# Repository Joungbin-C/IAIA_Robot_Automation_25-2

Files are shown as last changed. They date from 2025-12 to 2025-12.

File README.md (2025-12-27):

# 25-2 Robot Automation: Battery Winding Manipulation Automation

**Date:** 2025/12/27

**Author:** Joungbin Choi, Hyeongyu Seo, Inyeop Kim

**Advisor:** Professor YK Kim

**Github:** [repository link](https://github.com/Joungbin-C/IAIA_Robot_Automation_25-2)

***

[**Demo Video**](https://youtu.be/vMVNzXjdA7o)

[**Report Link**](https://github.com/Joungbin-C/IAIA_Robot_Automation_25-2/tree/main/Report)

[**Source Code Link**](https://github.com/Joungbin-C/IAIA_Robot_Automation_25-2/tree/main/src)

[**Summary PPT Link**](https://github.com/Joungbin-C/IAIA_Robot_Automation_25-2/tree/main/Docs(PPT))

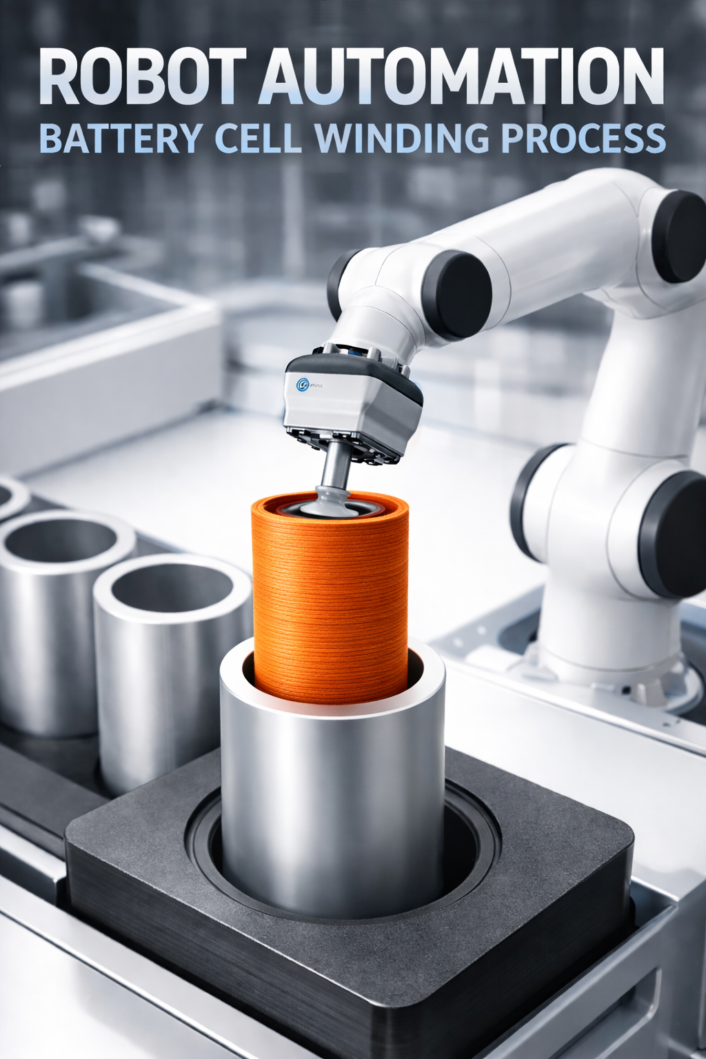
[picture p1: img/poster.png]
poster


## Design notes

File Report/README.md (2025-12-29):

# 25-2 Robot Automation: Battery Winding Manipulation Automation

**Date:** 2025/12/27

**Author:** Joungbin Choi, Hyeongyu Seo, Inyeop Kim

**Advisor:** Professor YK Kim

**Github:** [repository link](https://github.com/Joungbin-C/IAIA_Robot_Automation_25-2)

**Demo Video:** [**Demo Video**](https://youtu.be/vMVNzXjdA7o)

***

## I. Introduction

With the rapid growth of the electric vehicle (EV) market, the secondary battery industry has emerged as a key strategic sector. It is projected that by 2030, electric vehicles will account for more than 40% of the global automotive market, leading to a significant increase in battery production demand[1]. However, conventional battery cell assembly and disassembly processes remain highly dependent on manual labor, resulting in limitations in productivity, process consistency, and quality control. In particular, as the importance of battery recycling and safe disassembly increases, there is a growing demand for intelligent automation systems capable of handling precise and complex operations beyond simple assembly tasks.

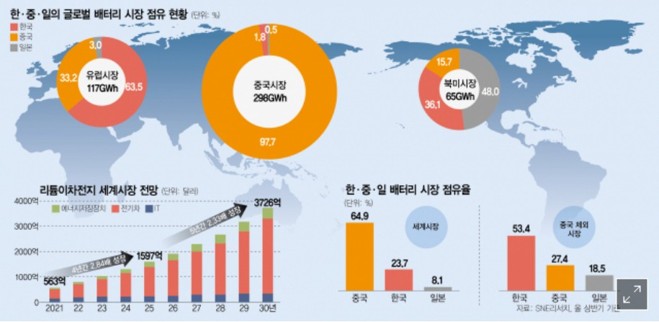
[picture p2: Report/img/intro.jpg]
intro


This project aims to address these challenges by developing an **automated battery cell winding process using industrial robots integrated with machine vision and artificial intelligence technologies**. By combining robotic manipulation, sensor-based detection nodes, state diagram–based control logic, and camera-based recognition of battery cells and winding components, the project seeks to transform a labor-intensive process into a high-speed, high-precision automated system. Through this approach, the feasibility of improving productivity, reliability, and safety in battery manufacturing and recycling processes is investigated.

## II. Problem Statement

### 1. Project Objectives

The main objectives of this project are as follows:

1. **Implementation of Automated Assembly and Disassembly of Battery Cell Winding Processes**
   To automate the assembly and disassembly of battery cells and winding components using industrial robots, thereby minimizing human error and improving repeatability.
2. **Development of a Machine Vision–Based Recognition System**
   To detect battery cell positions, orientations, and conditions (normal or defective) using camera-based vision systems and AI models, and to integrate the recognition results into the robot control system.
3. **Design of Robot Control Logic and State Diagrams**
   To design structured state diagrams that manage process flow and ensure stable coordination between sensor detection nodes and robotic actions.
4. **Verification of Process Reliability and Performance**
   To experimentally evaluate the success rate, accuracy, and operational stability of the automated system and assess its applicability to real industrial environments.

### 2. Expected Outcomes

The expected outcomes of this project are as follows:

1. **Improved Productivity and Operational Efficiency**
   By replacing manual labor with robotic automation, continuous operation beyond traditional working hours becomes possible, significantly increasing overall productivity.
2. **Enhanced Accuracy and Quality Consistency**
   The automated system is expected to achieve a high success rate in assembly and disassembly tasks, while the machine vision system enables reliable identification of normal and abnormal battery cells, excluding specific inclusion cases.
3. **Reduced Labor Dependency and Improved Workplace Safety**
   Automating repetitive and potentially hazardous battery handling processes reduces worker exposure to risk and lowers dependence on skilled manual labor.
4. **Scalability for Battery Recycling and Future Smart Factory Applications**
   The proposed system can be extended to battery disassembly and recycling processes, providing a technological foundation for advanced smart factory and sustainable battery production systems.

### 3. Evaluation Index

| Process | Target |
| --- | --- |
| **UR5 Robot Operation** | - Bracket detection success rate ≥ 98% <br />- Cell box detection success rate = 100% <br />- Pick and Place success rate ≥ 95% <br />- Stopper linkage success rate = 100% <br />- Assembly/Disassembly process completion time ≤ 1 minute |
| **Indy10 Robot Operation** | - Cell orientation detection success rate = 100% <br />- Foreign object detection success rate ≥ 95% <br />- Defective cell detection success rate ≥ 95% <br />- Stopper linkage success rate = 100% <br />- Winding assembly/disassembly process completion time ≤ 1 minute |
| **Defect Detection** | - Defect detection success rate (cylindrical surface) ≥ 95% <br />- Defect detection success rate (flat surface) ≥ 80% |

### 4. Hardware

materials

These are materials for manipulation. A bracket is moving with slide rail and cells will be putted on it. Lastly, winds will be assembled or disassembled with cells. 

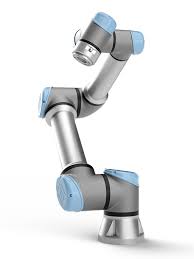
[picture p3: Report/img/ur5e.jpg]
ur5e


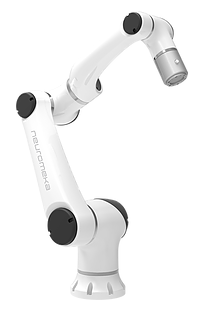
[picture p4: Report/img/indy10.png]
indy10


UR5e(upper image) and Indy10(bottom image) are utilized for assembling and disassembling manipulation. Overall, UR5e is used to pick-and-place cells on the bracket or get off cells from bracket. Indy10 is used to assemble or disassemble winds from cells. If there is a defected cell, Indy10 get rid of it from the bracket. 

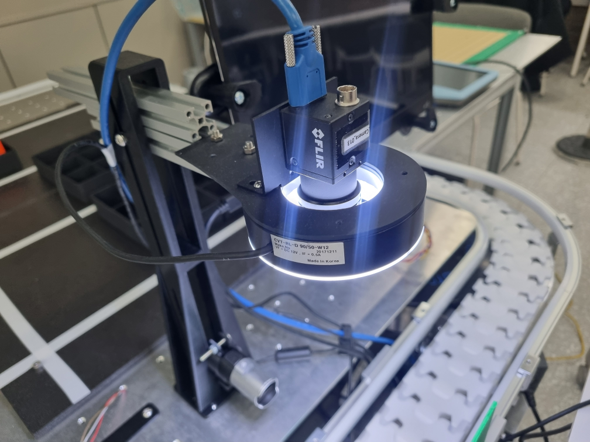
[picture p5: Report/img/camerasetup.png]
camerasetup


This is setup for machine vision to check the state of cells. There are two machine vision cameras: top-view and side-view. Top view camera checks for a circularity of cells and side camera checks for defects on the side of cells.

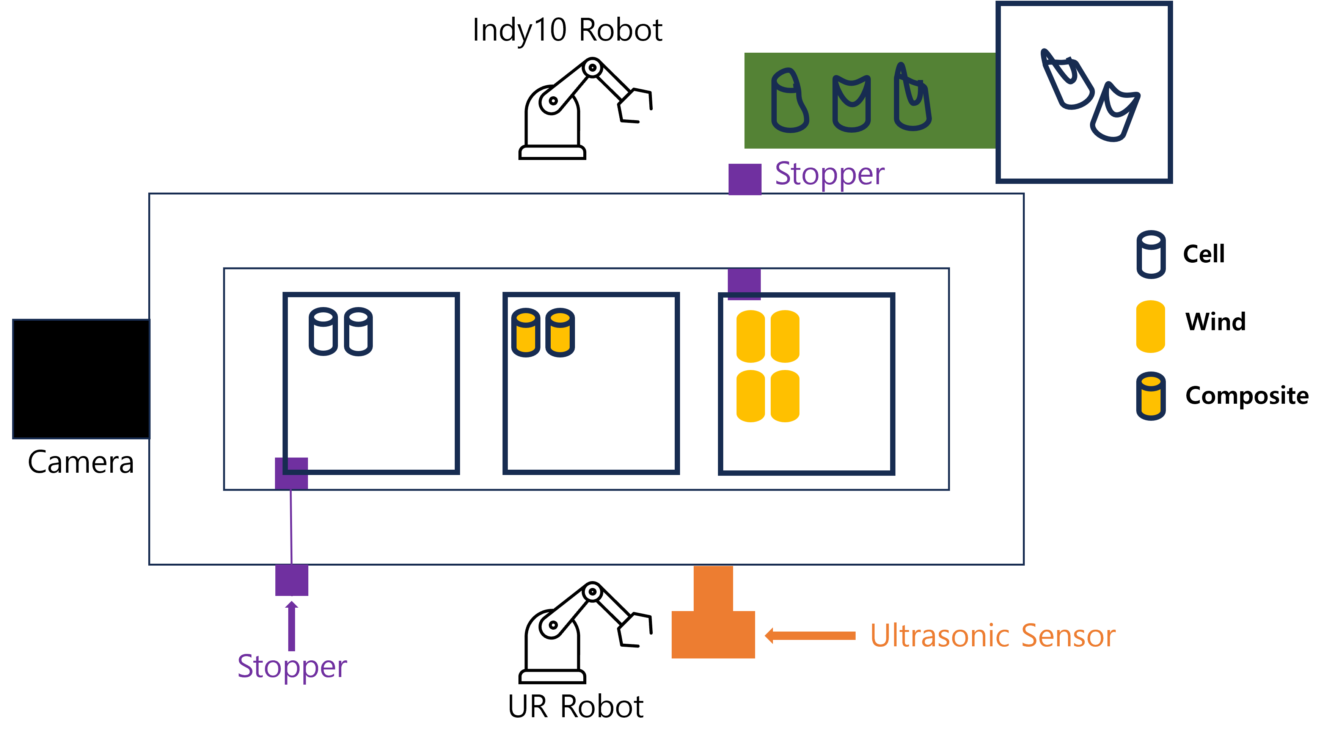
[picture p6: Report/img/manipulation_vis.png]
manipulation_vis


This is overall setup for battery wind manipulation. 

## III. Individual Report
**[UR5e](https://github.com/Joungbin-C/IAIA_Robot_Automation_25-2/tree/main/Report/Report_(Dis)assembly_Automation_Process/Report_(Dis)Assembly_Automation.md)**

**[Indy10](https://github.com/Joungbin-C/IAIA_Robot_Automation_25-2/blob/main/Report/Report_(De)Compose_process/Report_(De)Compose_process.md)**

**[Machine Vision](https://github.com/Joungbin-C/IAIA_Robot_Automation_25-2/blob/main/Report/Report_MachineVision_Process/Report_MachineVision_Process.md)**

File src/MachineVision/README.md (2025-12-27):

# Windows에서 PySpin 가상환경 설치 가이드

## 0. 사전 준비

1. **카메라 드라이버 & Spinnaker SDK 설치**
   - PySpin 버전과 **동일한 버전의 Spinnaker SDK**를 먼저 설치
   - 예: PySpin 3.0.0.0 → **Spinnaker SDK 3.0.0.0**
   - [PySpin 및 SDK 다운로드 링크](https://www.teledynevisionsolutions.com/ko-kr/support/support-center/software-firmware-downloads/iis/download-the-latest-spinnaker-software-development-kit/spinnaker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)
2. **Python 버전 확인**
   - 지원 버전: **3.5 ~ 3.8, 3.10**
   - 권장: **Python 3.10 (64-bit)** (우분투 20.04이면 3.8 (64-bit) 추천)
   - Python 설치 시 반드시 **64-bit**로 설치
   - 환경 변수에 파이썬이 등록 되어있어야함

------

## 1. Python 설치 확인

```
python --version
```

또는 Python 3.10 명시:

```
py -3.10 --version

# Ubuntu Version
py -3.8 --version
```

------

## 2. 콘다 설치

이 가이드에선 콘다가 미리 설치 되었다는 가정으로 진행

------

## 3. 가상환경 생성 (conda)

Python 3.10 기준 예시:

```
conda create -n pyspin python=3.10 -y

# Ubuntu Version
conda create -n pyspin python=3.8 -y
```

------

## 4. 가상환경 활성화

```
conda activate pyspin
```

성공하면 프롬프트 앞에 `(pyspin)` 표시됨:

```
(pyspin) C:\pyspin_project>
```

------

## 5. pip 최신화

```
python -m ensurepip
python -m pip install --upgrade pip
```

------

## 6. PySpin Wheel 설치

### PySpin wheel 파일 준비

Wheel 파일 위치로 이동

```
cd C:\path\to\spinnaker_python_wheel
```

whl파일 확인

예시:

```
spinnaker_python-3.0.0.0-cp310-cp310-win_amd64.whl
```

반드시 확인:

- `cp310` → Python 3.10
- `win_amd64` → 64-bit Windows

Unbuntu 20.04이면:
- `cp38` → Python 3.8
- 'linux_x86_64` → 64-bit Linux

### 설치

```
pip install spinnaker_python-3.x.x.x-cp310-cp310-win_amd64.whl
```

(실제 파일명으로 변경)

------

## 7. 설치 확인

```
python -c "import PySpin; print(PySpin.__version__)"
```

에러 없으면 성공

------

## 8. 예제 실행

Spinnaker SDK 또는 PySpin 압축 안의 예제 사용:

```
python Examples\Python3\Acquisition.py
```

또는 직접 테스트:

```
import PySpin

system = PySpin.System.GetInstance()
cam_list = system.GetCameras()
print("Number of cameras:", cam_list.GetSize())

cam_list.Clear()
system.ReleaseInstance()
```

------

## 9. 프로젝트를 위한 환경 설치

```
pip install numpy==2.2.6
pip install opencv-python-headless==4.10.0.84
pip install ultralytics==8.3.232
pip install PyQt5==5.15.11
pip install Pillow==9.2.0
```

## 10. 코드 실행 방법

깃허브에 `src/MachineVsion/AcquireAndDisplay_Final.py`을 spinnaker_python 파일에서 `Examples/Python3`에 옮긴 후 실행

## 11. 환경 비활성화

```
deactivate
```

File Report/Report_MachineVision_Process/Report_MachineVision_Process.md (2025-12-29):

# 25-2 Robot Automation - Machine Vision(Cell Defect Detecting)

**Date:** 2025/12/25

**Author:** Joungbin Choi

**Github:** [repository link](https://github.com/Joungbin-C/IAIA_Robot_Automation_25-2/tree/main)

**Demo Video:** [Youtube link](https://youtu.be/vMVNzXjdA7o)

***

## I. Introduction

With the rapid growth of the electric vehicle (EV) market, the secondary battery industry has emerged as a key strategic sector. It is projected that by 2030, electric vehicles will account for more than 40% of the global automotive market, leading to a significant increase in battery production demand[1]. However, conventional battery cell assembly and disassembly processes remain highly dependent on manual labor, resulting in limitations in productivity, process consistency, and quality control. In particular, as the importance of battery recycling and safe disassembly increases, there is a growing demand for intelligent automation systems capable of handling precise and complex operations beyond simple assembly tasks.

This project aims to address these challenges by developing an **automated battery cell winding process using industrial robots integrated with machine vision and artificial intelligence technologies**. By combining robotic manipulation, sensor-based detection nodes, state diagram–based control logic, and camera-based recognition of battery cells and winding components, the project seeks to transform a labor-intensive process into a high-speed, high-precision automated system. Through this approach, the feasibility of improving productivity, reliability, and safety in battery manufacturing and recycling processes is investigated.

## II. Problem Statement

### 1. Project Objectives

The main objectives of this project are as follows:

1. **Implementation of Automated Assembly and Disassembly of Battery Cell Winding Processes**
    To automate the assembly and disassembly of battery cells and winding components using industrial robots, thereby minimizing human error and improving repeatability.
2. **Development of a Machine Vision–Based Recognition System**
    To detect battery cell positions, orientations, and conditions (normal or defective) using camera-based vision systems and AI models, and to integrate the recognition results into the robot control system.
3. **Design of Robot Control Logic and State Diagrams**
    To design structured state diagrams that manage process flow and ensure stable coordination between sensor detection nodes and robotic actions.
4. **Verification of Process Reliability and Performance**
    To experimentally evaluate the success rate, accuracy, and operational stability of the automated system and assess its applicability to real industrial environments.

### 2. Expected Outcomes

The expected outcomes of this project are as follows:

1. **Improved Productivity and Operational Efficiency**
    By replacing manual labor with robotic automation, continuous operation beyond traditional working hours becomes possible, significantly increasing overall productivity.
2. **Enhanced Accuracy and Quality Consistency**
    The automated system is expected to achieve a high success rate in assembly and disassembly tasks, while the machine vision system enables reliable identification of normal and abnormal battery cells, excluding specific inclusion cases.
3. **Reduced Labor Dependency and Improved Workplace Safety**
    Automating repetitive and potentially hazardous battery handling processes reduces worker exposure to risk and lowers dependence on skilled manual labor.
4. **Scalability for Battery Recycling and Future Smart Factory Applications**
    The proposed system can be extended to battery disassembly and recycling processes, providing a technological foundation for advanced smart factory and sustainable battery production systems.

### 3. Evaluation Index

| Process | Target |
| --- | --- |
| **UR5 Robot Operation** | - Bracket detection success rate ≥ 98% <br />- Cell box detection success rate = 100% <br />- Pick and Place success rate ≥ 95% <br />- Stopper linkage success rate = 100% <br />- Assembly/Disassembly process completion time ≤ 1 minute |
| **Indy10 Robot Operation** | - Cell orientation detection success rate = 100% <br />- Foreign object detection success rate ≥ 95% <br />- Defective cell detection success rate ≥ 95% <br />- Stopper linkage success rate = 100% <br />- Winding assembly/disassembly process completion time ≤ 1 minute |
| **Defect Detection** | - Defect detection success rate (cylindrical surface) ≥ 95% <br />- Defect detection success rate (flat surface) ≥ 80% |

## III. Requirements

Write a list of HW/SW requirements.

### 1. Hardware List

* Computer
* 2 Spinnaker Cameras
* Slide Rail
* 2 Stepper Motors
* 2 Ardunio Boards
* 2 Ultrasonic Sensors
* Windings, Cells, Brakets
* Light

### 2. Software List

* CUDA 13.0
* cudatoolkit 12.6
* Python 3.10.8
* Pytorch 2.7.0+cu128
* YOLO v8
* Spinnaker SDK
* Spinnaker Python
* Numpy 2.2.6
* opencv python headless 4.10.0.84
* ultralytics 8.3.232
* PyQT5 5.15.11
* Pillow 9.2.0

### 3. Dataset

For surface detection of the cell, the dataset is customized. There are 4 classes: rugged, pitted, inclusion, and scratch

**Dataset link:** [download link](https://universe.roboflow.com/jb-edsws/surface-detecting-bdnua/dataset/2) 

***

## IV. Installation and Procedure

### 1. Hardware Setup

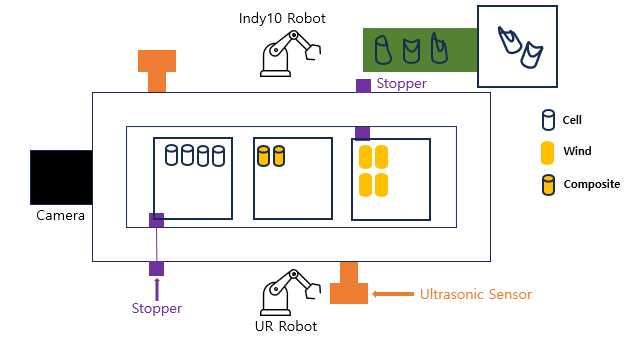
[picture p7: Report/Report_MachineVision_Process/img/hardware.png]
hardware


**Figure 1. Hardware Overview**

This image show hardware Setup:

1. UR5 and Indy10 robots are placed between the stopper(stepper motors) and ultrasonic sensors. If ultrasonic sensors detect the bracket, stopper is closed.
2. Cameras are placed upper and side of the rail. Upper camera check the circularity of the cell and side camera check the surface of the cell.

camerasetup

**Figure 2. Camera Setup**

### 2. Software Installation

For software installation of machine vision part, you can find the instruction in this [github link](https://github.com/Joungbin-C/IAIA/tree/main/Project/Project2_RobotAutomation)

### 3. Data Preparation

This dataset is customized and total number of data is 1,701.

train data : 90%

validation data : 7% 

test data : 3%

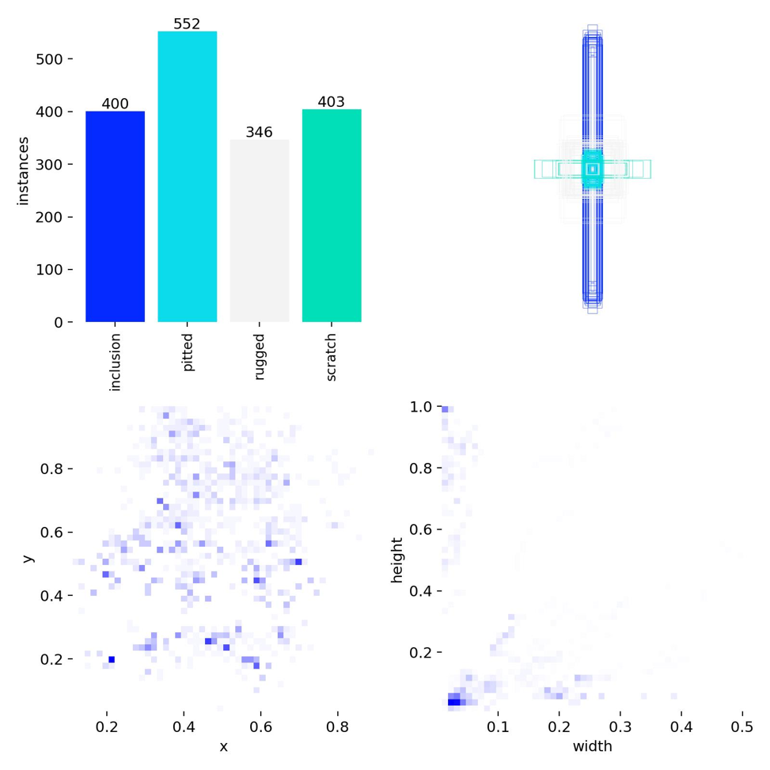
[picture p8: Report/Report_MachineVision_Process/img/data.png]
data


**Figure 3. Dataset Distribution**

The original data was unbalanced. Inclusion and scratch are much less than others, so oversampling was proceeded. Final balanced dataset is shown in **Figure 3**.

### 4. Train model

YOLO (You Only Look Once) is a real-time object detection model that simultaneously performs object localization and classification in a single forward pass of a neural network. By processing the entire image at once rather than using a multi-stage detection pipeline, YOLO achieves high inference speed with relatively low computational complexity. The model divides the input image into a grid and predicts bounding boxes, confidence scores, and class probabilities for each grid cell, enabling efficient and accurate object detection. Due to its fast response time and robustness, YOLO is widely used in applications such as industrial automation, robotic pick-and-place systems, defect detection, and real-time machine vision–based control systems[2].

**Table 1. Hyperparameter of Surface Defect Detection Model**

| Parameter | Number |
| --- | --- |
| Model | YOLOv8s |
| Epoch | 100 |
| Batch | 8 |
| Optimizer | AdamW(lr=0.001) |
| Early Stop  | 20 |
| Final Epoch | 53 |

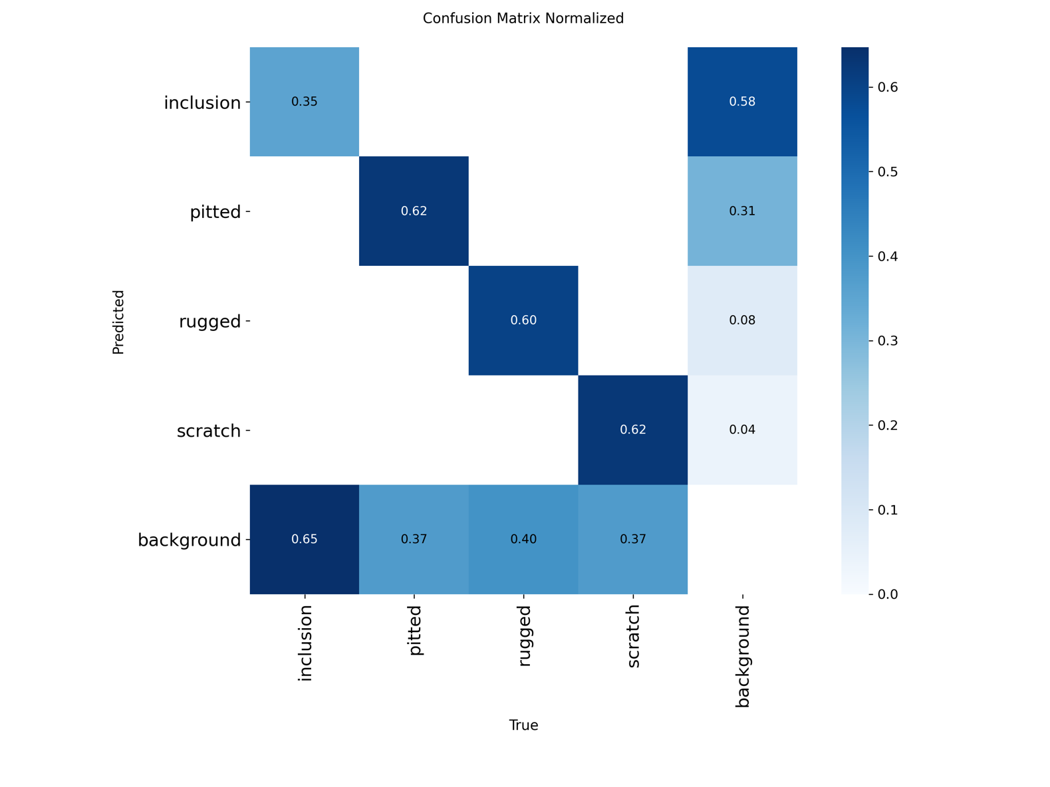
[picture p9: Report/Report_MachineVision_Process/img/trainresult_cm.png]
trainresult_cm


**Figure 4. Training Result Confusion Matrix**

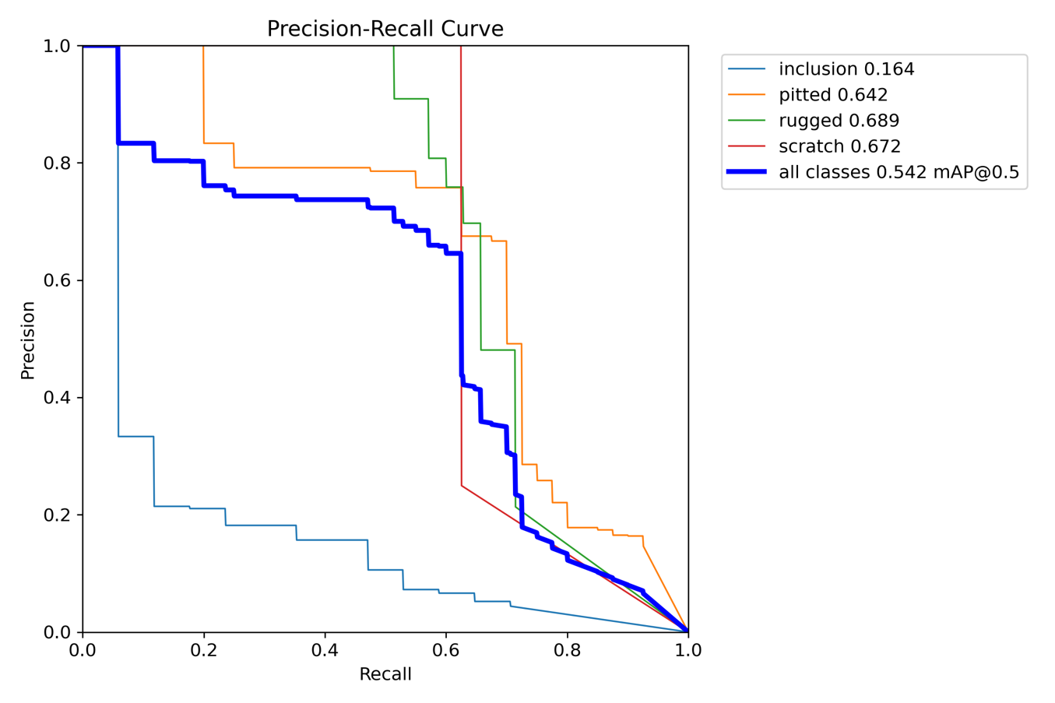
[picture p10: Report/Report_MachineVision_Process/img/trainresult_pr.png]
trainresult_pr


**Figure 5. PR Curve Graph**

**Table 2. Defect Classes**

| Class | Description |
| --- | --- |
| Rugged | Rough surfeace |
| Pitted | Indented defect |
| Inclusion | Foreign inclusion |
| Scratch | Scratch defect |

Thin and elongated inclusion defects are difficult to detect because their small size, low contrast, and extreme aspect ratios are poorly represented in bounding box–based object detection models, leading to feature loss and insufficient learning during training[5].

***

## V. Method

### 1. Overview

This study proposes an automated battery cell inspection system that integrates a **dual-camera machine vision setup with traditional image processing techniques and a deep learning–based surface defect detection model**. The system consists of two industrial FLIR cameras, OpenCV-based geometric analysis, a YOLO-based deep learning model, and a socket-based communication interface for external device control.

Camera 1 is responsible for **cell geometry analysis**, including circular shape detection, edge-based crack inspection, and thickness measurement. Camera 2 performs **surface defect detection** using a YOLO-based object detection model. The inspection process follows a state-based logic in which two consecutive cells (Cell 1 and Cell 2) are evaluated and their results are combined to generate a final decision flag.

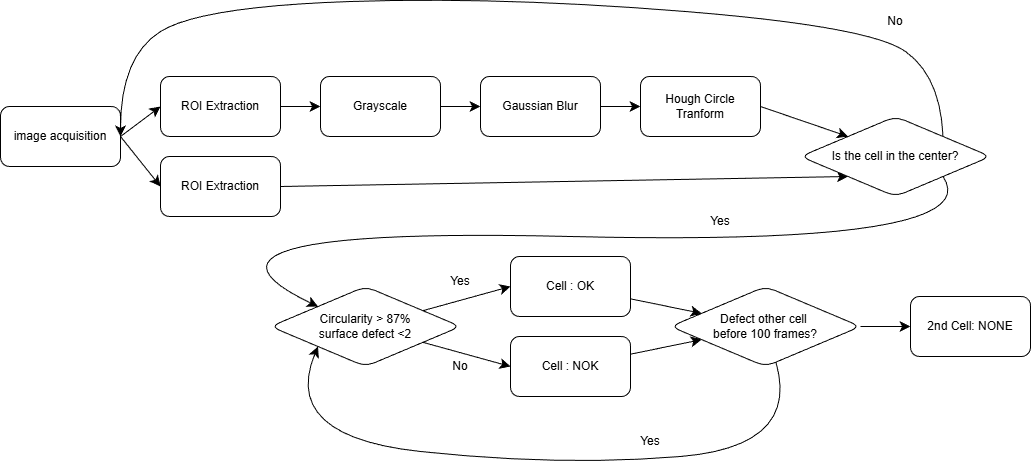
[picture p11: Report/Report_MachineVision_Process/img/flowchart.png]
flowchart


**Figure 6. Flow Chart**

### 2. Preprocessing

Preprocessing steps were designed separately for each camera according to its inspection purpose.

For Camera 1, a fixed-size **region of interest (ROI)** centered in the image was extracted to remove unnecessary background information. The ROI image was converted to grayscale and smoothed using Gaussian blur to reduce noise. Circular features of the battery cell were detected using the **Hough Circle Transform**, and the detected outer circle was used to define an edge ring region. **Canny edge detection** was applied within this region to emphasize crack-related features[3]. 

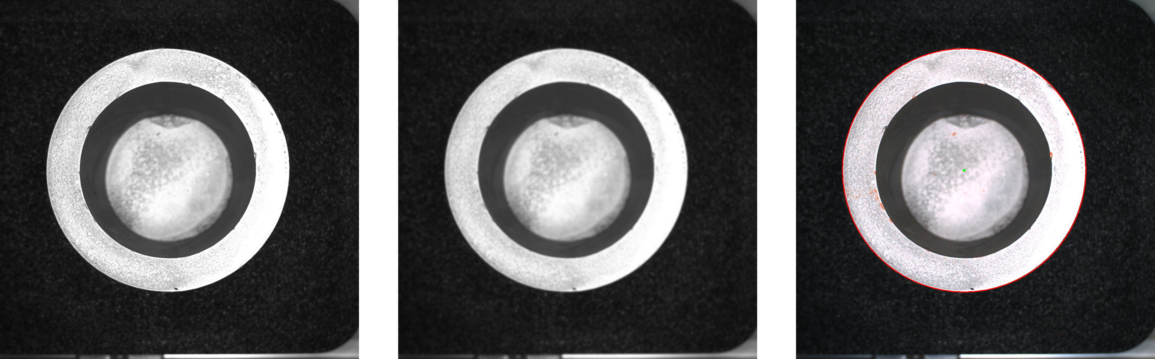
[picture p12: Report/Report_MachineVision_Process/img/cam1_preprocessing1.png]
cam1_preprocessing1


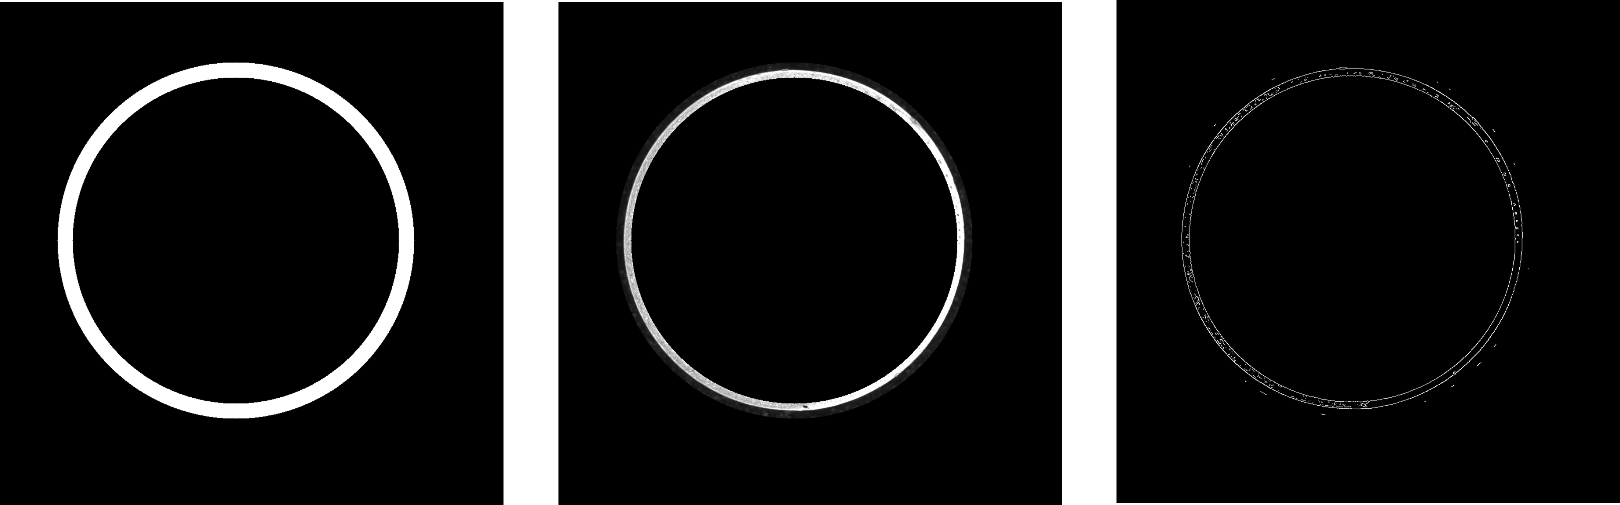
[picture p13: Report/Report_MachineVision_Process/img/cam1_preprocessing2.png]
cam1_preprocessing2


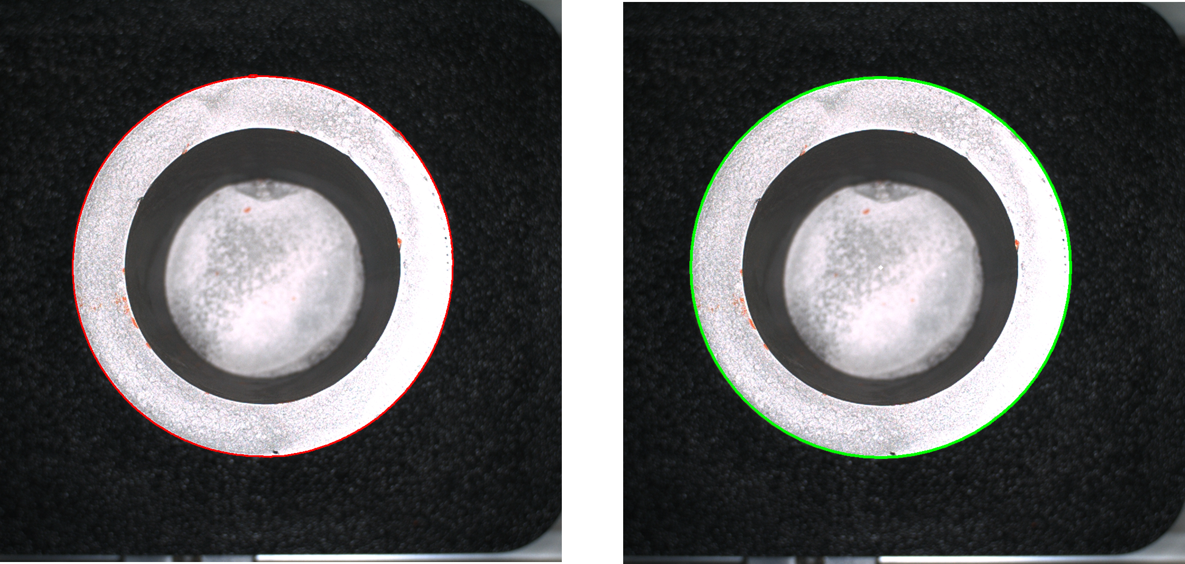
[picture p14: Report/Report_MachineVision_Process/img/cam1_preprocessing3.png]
cam1_preprocessing3


**Figure 7. Preprocessing: Grayscale, Gaussian blur, Hough Circle,  Ring Mask, Ring ROI, Canny Edge,  Contour, and Result**

Contour extraction and circularity analysis were then used to determine the presence of edge cracks.
$$
Circularity= \frac{4πA} {P^2}
$$
For Camera 2, a centered ROI was extracted from the original color image and directly passed to the YOLO model without additional color conversion. This approach preserves surface texture and intensity variations, which are critical for surface defect detection. Input resizing and normalization were handled internally by the YOLO framework.

### 3. Deep Learning Model

A **YOLOv8-based object detection model** was employed for surface defect detection[4]. YOLO (You Only Look Once) is a single-stage object detection framework that simultaneously predicts object locations and class probabilities in a single forward pass, enabling real-time performance.

cam2_result (2)

**Figure 8. Surface Detection Result**

YOLOv8 offers improved detection accuracy and computational efficiency compared to previous YOLO versions, making it suitable for real-time industrial inspection systems. In this study, a fine-tuned YOLOv8 model trained on a battery surface defect dataset was used. The model outputs bounding boxes and confidence scores for detected surface defects, and the number of detected defects is used as a criterion for surface quality assessment.

### 4. Postprocessing

#### **Algorithm #1: Cell Geometry and Edge-Based Defect Decision**

The first postprocessing algorithm evaluates the geometric validity of the detected battery cell and determines edge-related defects. The detected outer circle must satisfy predefined radius and area thresholds to be considered valid. An edge ring region is then analyzed using contour-based circularity metrics to identify potential cracks. Final decisions are made only when the detected cell is sufficiently centered in the image, reducing false detections caused by partial or misaligned cells.

#### **Algorithm #2: Cell Pairing and Decision Fusion Algorithm**

The second algorithm fuses the inspection results of two consecutive cells (Cell 1 and Cell 2). Each cell is classified as OK or NOK, and their combined results are mapped to predefined numeric flags for external communication. A timeout mechanism is implemented to handle cases where the second cell is not detected within a specified number of frames, ensuring robust operation in continuous production environments.

### 5. Experiment Method

Experiments were conducted under continuous image acquisition conditions that simulate real industrial inspection environments. Two FLIR cameras were operated in continuous acquisition mode, and multiple samples of normal and defective battery cells were tested.

The evaluation metrics included:

- Circle detection success rate
- Surface defect detection success rate using YOLO

## VI. Results and Analysis

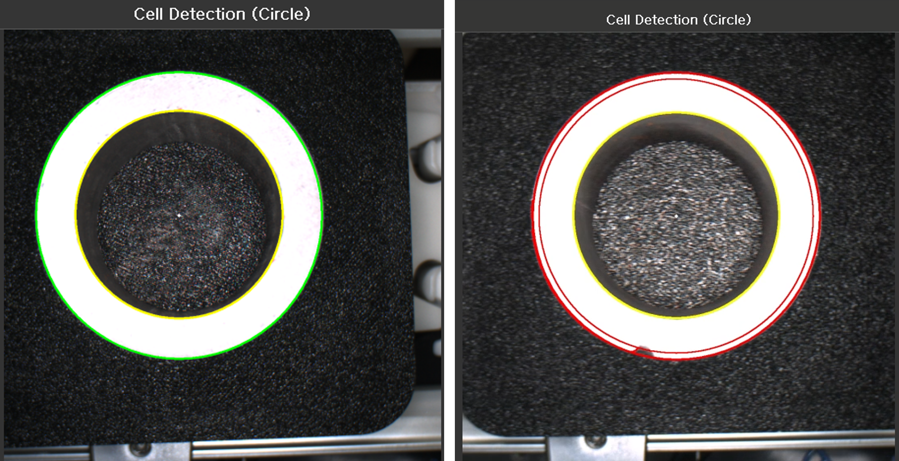
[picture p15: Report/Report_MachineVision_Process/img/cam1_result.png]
cam1_result


**Figure 9. Top Camera Result**

The accuracy of the circularity-based decision logic was evaluated through a total of 105 inspection trials. Among these, 53 defective cells and 52 normal cells were passed through the system to verify the correctness of the classification results. The experimental results showed that both normal cells (Cell Okay) and defective cells (Cell Not Okay) achieved accuracy levels exceeding the target threshold of 95%. This indicates that the circularity-based decision method provides high reliability and robustness for detecting edge cracks on battery cells. In particular, the method maintained consistent performance even under conditions with image noise and variations in illumination.

**Table 3. Circularity Accuracy Table**

| Classification | Target Accuracy [%] | Detection Result | Result Accuracy [%] |
| --- | --- | --- | --- |
| Cell Okay | ≥ 95 | 102 / 105 | **97.14** |
| Cell Not Okay  | ≥ 95 | 100 / 105 | **95.24** |

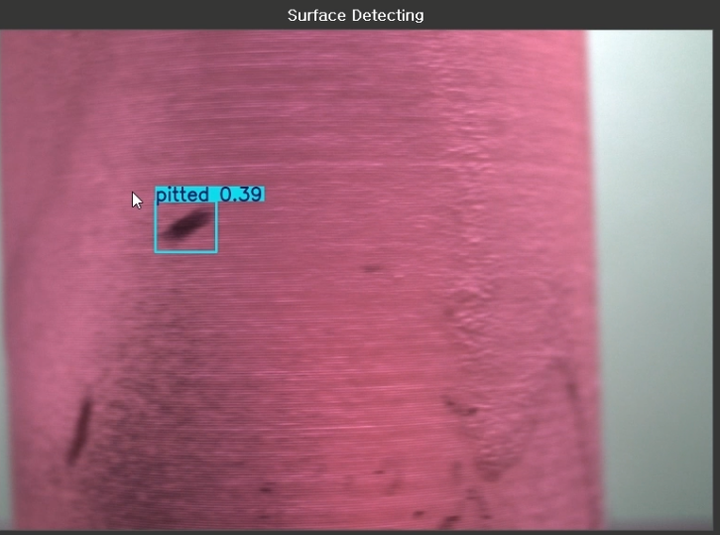
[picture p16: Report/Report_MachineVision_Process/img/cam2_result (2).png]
cam2_result (2)


**Figure 10. Side Camera Result**

For surface defect detection, the success rate was recorded by passing 50 samples for each defect class through the system. The results showed that the Pitted, Rugged, and Scratch defect classes all satisfied the target accuracy of 80% or higher. Among them, the Pitted defect achieved a notably high detection success rate of 94%. This performance can be attributed to the relatively large defect area and the clear texture contrast between the defect and the surrounding surface, which allowed the YOLO model to learn discriminative features effectively.

In contrast, the Inclusion defect exhibited a significantly lower detection success rate of 48%, failing to meet the target performance. Inclusion defects typically have thin and elongated shapes, low contrast relative to the surface, and high variability in appearance. As a result, feature information is often lost in bounding box–based object detection models, leading to poor detection performance. This outcome highlights a structural limitation of YOLO-based models when applied to small and slender defect types.

**Table 4. Side Defect Detection Accuracy Table**

| Defect Type | Target Accuracy [%] | Detection Result | Result Accuracy [%] |
| --- | --- | --- | --- |
| Inclusion | ≥ 80 | 24 / 50 | **48** |
| Pitted | ≥ 80 | 47 / 50 | **94** |
| Rugged | ≥ 80 | 43 / 50 | **86** |
| Scratch | ≥ 80 | 43 / 50 | **86** |

***

## VII. Conclusion

This project presented an automated battery cell inspection system that combines image processing and deep learning techniques. A dual-camera setup was used, where one camera performed cell shape inspection using circularity analysis, and the other camera detected surface defects using a YOLO-based model.

The circularity-based inspection showed reliable performance, achieving accuracy above the target value of 95% for both normal and defective cells. This result confirms that the proposed method is effective for detecting edge cracks under various imaging conditions. For surface defect detection, the YOLO model successfully detected Pitted, Rugged, and Scratch defects with accuracy higher than the target of 80%. However, the detection performance for Inclusion defects was relatively low due to their thin shape and low contrast.

In addition, the performance observed during testing was higher than that indicated by the confusion matrix obtained during training. This is because various data augmentation techniques such as adding noise and adjusting brightness were applied to the training dataset to improve robustness. In contrast, the real-world environment had fixed lighting and stable conditions, which resulted in higher detection accuracy.

Future work should focus on improving the detection of Inclusion defects by using higher-resolution images, more training data, or segmentation-based models. Additional experiments under different lighting conditions will also help improve the overall reliability of the system.

## Reference

[1] Y. Park, “Battery Industry Competition: Challenges for Korean Battery Companies amid China’s Rapid Growth,” *Seoul Economic Daily*, Nov. 17, 2024. Available: https://www.sedaily.com/NewsView/29X4QWC74S

[2] J. Redmon, S. Divvala, R. Girshick, and A. Farhadi, “You Only Look Once: Unified, Real-Time Object Detection,” *Proceedings of the IEEE Conference on Computer Vision and Pattern Recognition (CVPR)*, pp. 779–788, 2016.

[3] OpenCV, “OpenCV Documentation,” OpenCV Official Documentation. Available: https://docs.opencv.org

[4] Ultralytics, “YOLOv8 Documentation,” Ultralytics Official Documentation. Available: https://docs.ultralytics.com

[5] Y. Zhang, J. Yang, and Z. Liu, “Surface Defect Detection Based on Deep Learning: A Review,”
 *Journal of Manufacturing Systems*, vol. 62, pp. 682–695, 2022.

***

## Appendix

### 1. Team Contribution

| Name | Job Descriptions |
| --- | --- |
| Inyeop Kim | UR5 manipulation |
| HyeonGyu Seo  | Indy10 Manipulation |
| Joungbin Choi | Hardware, Machine Vision |

### 2. Combined Works

This report covers deep learning-based and machine vision cell defect detection.

Process recognition-based pick and place automation with Indy10 and UR5 are covered in the following links.

[Indy10](https://github.com/shg0873/IAIA/tree/main/Project/Project2_RobotAutomation/Report)

[UR5](https://github.com/Kiminyeop-cpu/Robot-Automation/blob/main/Battery%20Cell%20Winding%20Process.pdf)

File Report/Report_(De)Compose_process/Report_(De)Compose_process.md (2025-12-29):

# Project 2: Robot Automation

Industrial AI & Automation 2025

**Name:** Seo HyeonGyu

**Date:** 2025/12/25

**Github**: [Link](https://github.com/Joungbin-C/IAIA_Robot_Automation_25-2/tree/main)

[TOC]

____

## I. Introduction

With the rapid growth of the electric vehicle (EV) market, the secondary battery industry has emerged as a key strategic sector. It is projected that by 2030, electric vehicles will account for more than 40% of the global automotive market, leading to a significant increase in battery production demand. However, conventional battery cell assembly and disassembly processes remain highly dependent on manual labor, resulting in limitations in productivity, process consistency, and quality control. In particular, as the importance of battery recycling and safe disassembly increases, there is a growing demand for intelligent automation systems capable of handling precise and complex operations beyond simple assembly tasks.

This project aims to address these challenges by developing an **automated battery cell winding process using industrial robots integrated with machine vision and artificial intelligence technologies**. By combining robotic manipulation, sensor-based detection nodes, state diagram–based control logic, and camera-based recognition of battery cells and winding components, the project seeks to transform a labor-intensive process into a high-speed, high-precision automated system. Through this approach, the feasibility of improving productivity, reliability, and safety in battery manufacturing and recycling processes is investigated.

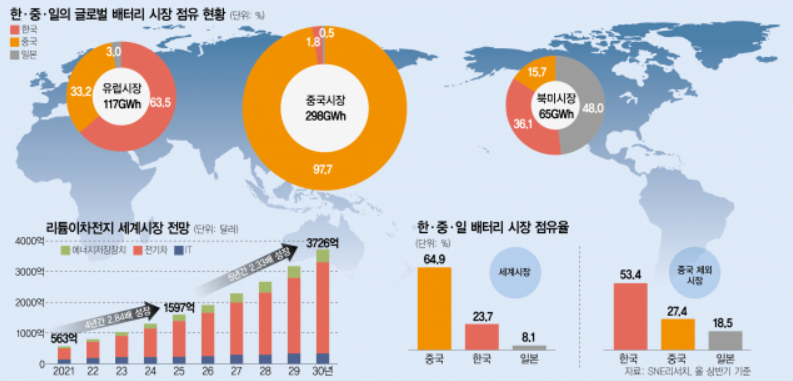
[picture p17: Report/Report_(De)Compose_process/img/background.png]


___________

## II. Problem Statement

### 1. Problems

1. Minor process deviations create potential defects, leading to battery failures and safety hazards.

2. In mass production, significant process variation creates challenges in ensuring uniformity.

3. Conventional defect inspection methods are slow and only detect surface defects.

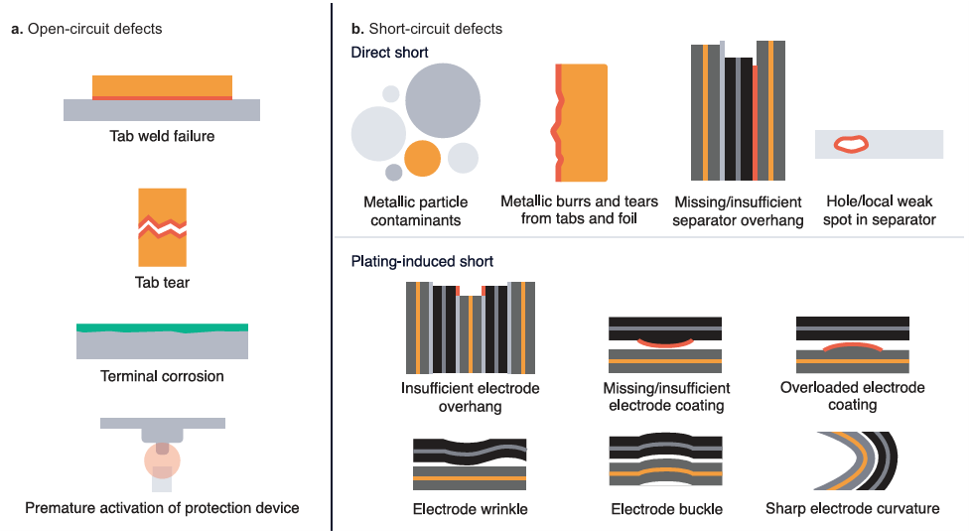
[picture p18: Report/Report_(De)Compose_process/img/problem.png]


### 2. Projective Objectives

The main objectives of this project are as follows:

1. **Implementation of Automated Assembly and Disassembly of Battery Cell Winding Processes**
    To automate the assembly and disassembly of battery cells and winding components using industrial robots, thereby minimizing human error and improving repeatability.
2. **Development of a Machine Vision–Based Recognition System**
    To detect battery cell positions, orientations, and conditions (normal or defective) using camera-based vision systems and AI models, and to integrate the recognition results into the robot control system.
3. **Design of Robot Control Logic and State Diagrams**
    To design structured state diagrams that manage process flow and ensure stable coordination between sensor detection nodes and robotic actions.
4. **Verification of Process Reliability and Performance**
    To experimentally evaluate the success rate, accuracy, and operational stability of the automated system and assess its applicability to real industrial environments.

### 3. Expected Outcomes

The expected outcomes of this project are as follows:

1. **Improved Productivity and Operational Efficiency**
    By replacing manual labor with robotic automation, continuous operation beyond traditional working hours becomes possible, significantly increasing overall productivity.
2. **Enhanced Accuracy and Quality Consistency**
    The automated system is expected to achieve a high success rate in assembly and disassembly tasks, while the machine vision system enables reliable identification of normal and abnormal battery cells, excluding specific inclusion cases.
3. **Reduced Labor Dependency and Improved Workplace Safety**
    Automating repetitive and potentially hazardous battery handling processes reduces worker exposure to risk and lowers dependence on skilled manual labor.
4. **Scalability for Battery Recycling and Future Smart Factory Applications**
    The proposed system can be extended to battery disassembly and recycling processes, providing a technological foundation for advanced smart factory and sustainable battery production systems.

### 4. Evaluation Index

For each process, 100 iterations of the test are applied to determine the process success rate threshold for each node and set this as the target.

| Process | Target |
| --- | --- |
| **UR5 Robot Operation** | - Bracket detection success rate ≥ 98% <br />- Cell box detection success rate = 100% <br />- Pick and Place success rate ≥ 95% <br />- Stopper linkage success rate = 100% <br />- Assembly/Disassembly process completion time ≤ 1 minute |
| **Indy10 Robot Operation** | - Cell orientation detection success rate = 100% <br />- Foreign object detection success rate ≥ 95% <br />- Defective cell detection success rate ≥ 95% <br />- Stopper linkage success rate = 100% <br />- Winding assembly/disassembly process completion time ≤ 1 minute |
| **Defect Detection** | - Defect detection success rate (cylindrical surface) ≥ 95% <br />- Defect detection success rate (flat surface) ≥ 80% |

_______

## III. Requirements

### 1. Hardware list

**Co-Robot**

- UR-5e
- Indy-10

**Grippers**

- 2-finger gripper
- Vacuum gripper
- Screw-driver

**Material**

* Wind
* Cell
* Bracket

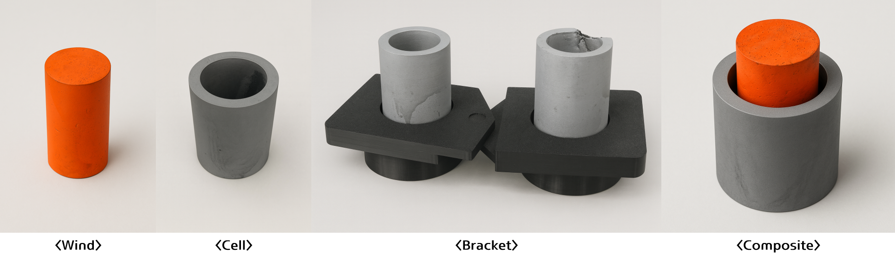
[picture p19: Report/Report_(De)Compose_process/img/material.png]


### 2. Software list

* Ubuntu 20.04
* Python 3.10.8
* Opencv
* Numpy

______________

## IV. Procedure

This report covers the camera-based cell and winding **disassembly and assembly automation process (UR robot)**.
- [disassembly and assembly automation](https://github.com/Joungbin-C/IAIA_Robot_Automation_25-2/tree/main/Report/Report_(Dis)assembly_Automation_Process/Report_(Dis)Assembly_Automation.md)

Process recognition-based **pick and place automation (Indy10)** and deep learning-based **cell defect detection** are covered in the following links.

* [pick and place automation]()
* [cell defect detection](https://github.com/shg0873/IAIA/tree/main/Project/Project2_RobotAutomation/Report)

### 1. Overview

The assembly process consists of two main stages: the winding process, and the defective cell detection process. During the winding process, the system identifies the bracket and the empty battery cell. Once the relative coordinates of the windings are detected, the components are assembled. This process also includes a defective cell detection mechanism, which classifies defective products based on flags received during operation.

The disassembly process focuses on removing the windings from the finished battery cell. Like the assembly process, this step also requires the detection of the bracket and the finished battery cell. Once the system detects the relative coordinates of the windings, the components are disassembled and placed into the empty winding box.

The entire process is illustrated in the flow chart below, and the goal of the entire process is to ensure high reliability through rigorous testing. The goal is to perform 100 repeat tests for each process. Based on these tests, a success rate threshold is established for each node, which serves as the target performance standard for the automated system.

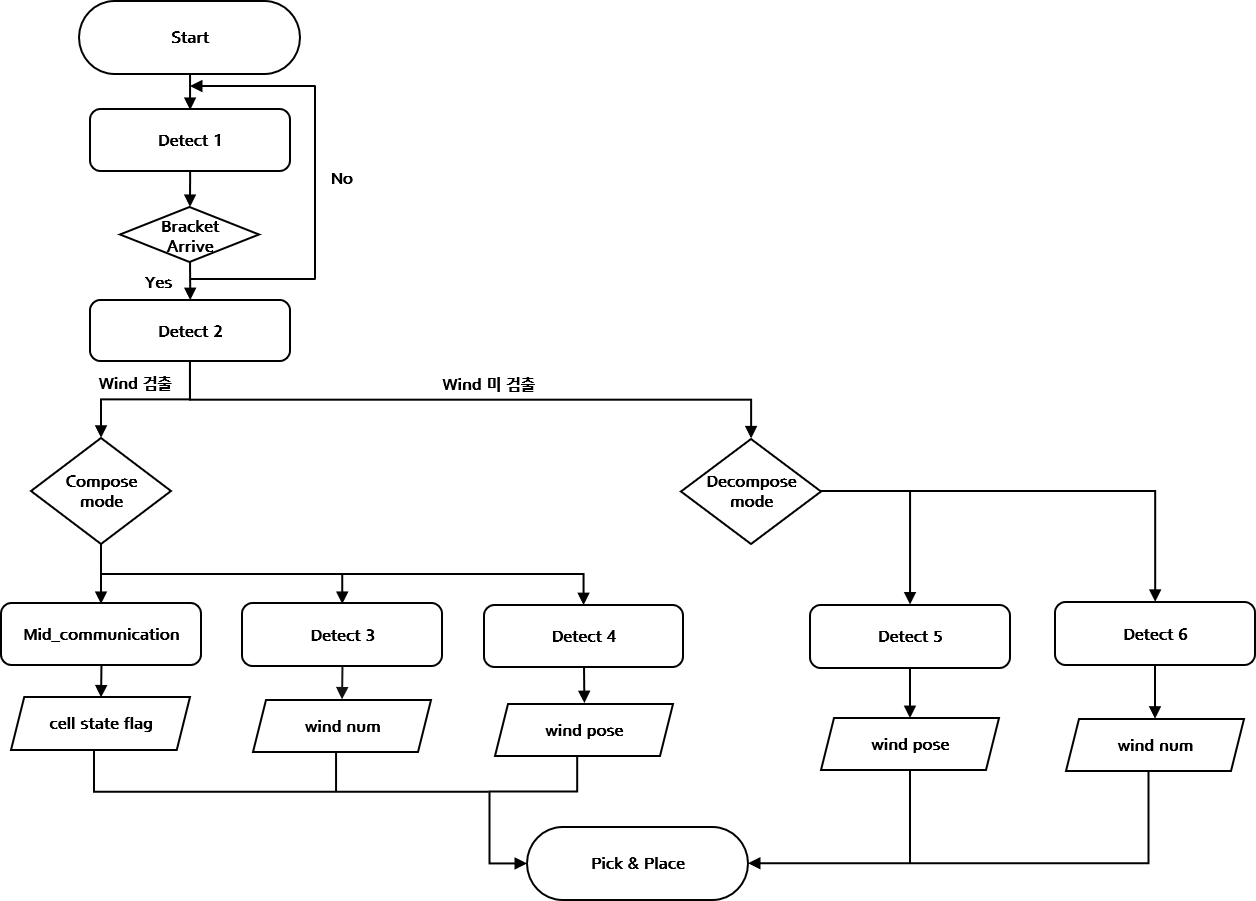
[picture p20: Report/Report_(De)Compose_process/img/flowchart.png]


You need to run the following nodes in the terminal in order and check the **index** of each device in the code when connecting the Arduino and camera.

```python
roscore

rosrun indy_driver camera.py

rosrun indy_driver Mid_image_display.py

rosrun indy_driver Mid_image_display2.py

rosrun indy_driver Mid_image_display3.py

rosrun indy_driver Mid_image_display4.py

rosrun indy_driver Mid_image_display5.py

rosrun indy_driver Mid_image_display6.py

rosrun indy_driver Mid_communication.py

roslaunch indy10_moveit_config moveit_planning_execution.launch robot_ip:=192.168.0.8
    
rosrun indy_driver Mid_project.py
```

### 2. Detection Node 1: Bracket detecting 

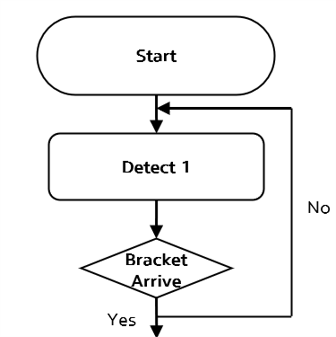
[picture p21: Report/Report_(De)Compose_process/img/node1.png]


The 1st node code is **Mid_image_display2**. This node determines whether a bracket has arrived. The presence of a bracket is determined by calculating the average intensity value using standard image processing techniques, taking advantage of the fact that the conveyor belt is white and the bracket is black. If the average intensity value falls below the threshold (150.0), a flag is set.

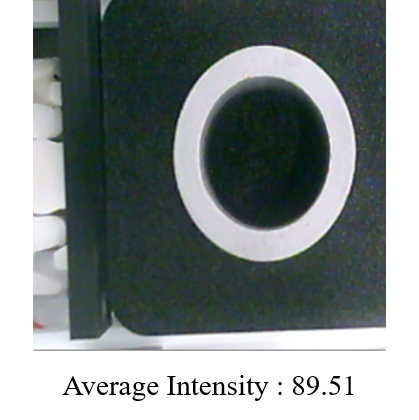
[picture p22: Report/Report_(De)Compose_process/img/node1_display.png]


### 3. Detection Node 2: Wind Detecting whether wind combined with cell

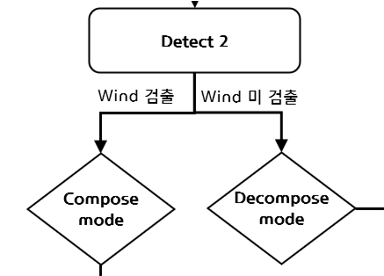
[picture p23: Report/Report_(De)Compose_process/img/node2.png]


The 2nd node code is **Mid_image_display4**. At this node, the process is determined by determining whether a winder is attached to the cell. If wind is detected through the classical image processing process below, the process proceeds to the disassembly process. If wind is not detected, the process proceeds to the attachment process.

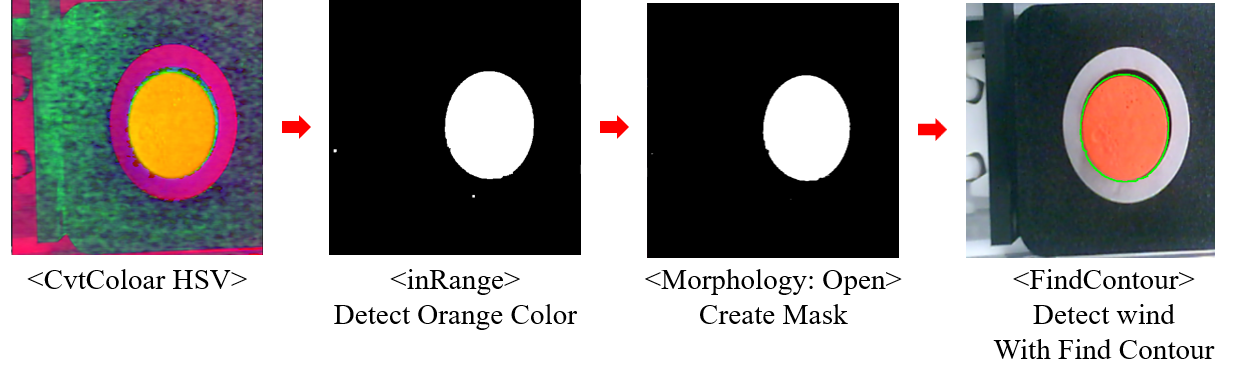
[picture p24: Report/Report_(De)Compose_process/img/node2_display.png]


### 4. Detection Node 3: Wind number detection during the composing process

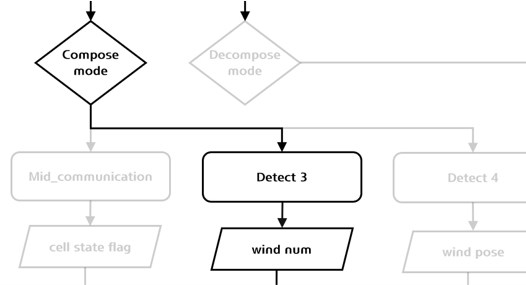
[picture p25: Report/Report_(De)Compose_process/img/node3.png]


The 3rd node code is **Mid_image_display1**. This node determines the wind number to be combined during the combination process. Through color detection, if the wind color exceeds a threshold, the box is determined to be filled with wind, and information on which wind number it is is passed to the indy10 robot. Starting from the left, the wind number information is 1, 2, 3 at the top, and 4, 5, 6 at the bottom.



###  5. Detection Node 4: Calculate the wind center During the composing process



The 4th node code is **Mid_image_display3**. In order to capture the wind to be combined with the cell in the combination process at the corresponding node, the relative coordinates of the wind center are calculated. The relative coordinates are obtained using the formula below after classical image processing, and the return value is the relative coordinates of the wind center [cm].



$$
x_{cm}=-(v-{M\over 2})\cdot {M\over H}
$$

$$
y_{cm}=-(u-{N\over2})\cdot{N\over W}
$$

* W denotes word width, H denotes word height
* N denotes image pixel width, M denotes image pixel height

### 6. Detection Node 5: Calculating the wind center during the decomposition process



The 5th node code is **Mid_image_display5**. At this node, the relative coordinates of the wind center are calculated to capture the wind to be separated from the cell during the decomposition process. The relative coordinates are obtained using the following formula after classical image processing, and the return value is the relative coordinates of the wind center [cm]. The formula is the same as for Node 4.

### 7. Detection Node 6: Wind number detection during the decomposition process



The 5th node code is **Mid_image_display6**.  This node determines the number at which to place the disassembled wind during the disassembly process. If the wind color is below a threshold through color detection, the box is determined to be empty and information on the number of the wind is passed to the indy10 robot. The wind numbers are 1, 2, 3 at the top, and 4, 5, 6 at the bottom, starting from the left.

____________

## V. Results

The test was performed a total of 100 times. Process time was measured from the moment the stopper contacts the bracket until the stopper opens at the end of the process.

| Part | Target | Result | Goal achievement |
| :--- | --- | --- | --- |
| Detecting part | - Cell orientation detection success rate = 100% | - 100% | O |
| Pick and Place and Defective<br /> Cell Erase | - Foreign object detection success rate ≥ 95% <br />- Defective cell detection success rate ≥ 95% | - 98%<br />- 99% | O |
| Stopper linkage and process <br />completion time | - Stopper linkage success rate = 100% <br />- Winding assembly/disassembly process <br />completion time ≤ 1 minute | - 100%<br />- Under 57[s] | O |

_____

## VI. Conclusion

This project developed an automated system for the battery cell winding assembly and disassembly process to address the increasing demand for batteries driven by the growth of the electric vehicle market and to address the productivity and safety issues inherent in existing manual processes. By integrating industrial robots and machine vision technology, we implemented an intelligent process that performs bracket and cell detection, defect detection, assembly, and disassembly. The system's reliability was verified through 100 repeated experiments. The results showed a 100% success rate in cell orientation detection and stopper linkage, and a 98% or higher success rate in foreign matter and defective cell detection, exceeding the targets in all evaluation indicators. Notably, by shortening the process completion time to less than 57 seconds, well below the target of one minute, this system proved to be an effective solution that can dramatically improve production efficiency and work safety in the battery manufacturing and recycling industries.

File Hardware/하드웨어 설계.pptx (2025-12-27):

## 하드웨어 설계

AIAI
22200757
최정빈
2025.09.30

## Base Plate


## Base Plate 도면


## Post Holder

프로파일 3030
프로파일 홀더


## Post & Post Holder


프로파일 3030
프로파일 홀더


## 조립


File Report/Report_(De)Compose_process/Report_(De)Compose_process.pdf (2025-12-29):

# Project 2: Robot Automation

Industrial AI & Automation 2025
Name: Seo HyeonGyu

Date: 2025/12/25
Github: Link (https://github.com/Joungbin-C/IAIA_Robot_Automation_25-2/tree/main)

Project 2: Robot Automation
I. Introduction
II. Problem Statement
1. Problems
2. Projective Objectives
3. Expected Outcomes
4. Evaluation Index
III. Requirements
1. Hardware list
2. Software list
IV. Procedure
1. Overview
2. Detection Node 1: Bracket detecting
3. Detection Node 2: Wind Detecting whether wind combined with cell
4. Detection Node 3: Wind number detection during the composing process
5. Detection Node 4: Calculate the wind center During the composing process
6. Detection Node 5: Calculating the wind center during the decomposition process
7. Detection Node 6: Wind number detection during the decomposition process
V. Results
VI. Conclusion

# I. Introduction

With the rapid growth of the electric vehicle (EV) market, the secondary battery industry has emerged as a key strategic sector. It is projected that by 2030, electric vehicles will account for more than 40% of the global automotive market, leading to a significant increase in battery production demand. However, conventional battery cell assembly and disassembly processes remain highly dependent on manual labor, resulting in limitations in productivity, process consistency, and quality control. In particular, as the importance of battery recycling and safe disassembly increases, there is a growing demand for intelligent automation systems capable of handling precise and complex operations beyond simple assembly tasks.
This project aims to address these challenges by developing an automated battery cell winding process using industrial robots integrated with machine vision and artificial intelligence technologies. By combining robotic manipulation, sensor-based detection nodes, state diagram– based control logic, and camera-based recognition of battery cells and winding components, the project seeks to transform a labor-intensive process into a high-speed, high-precision automated system. Through this approach, the feasibility of improving productivity, reliability, and safety in battery manufacturing and recycling processes is investigated.


# II. Problem Statement

## 1. Problems

1. Minor process deviations create potential defects, leading to battery failures and safety hazards.
2. In mass production, significant process variation creates challenges in ensuring uniformity.
3. Conventional defect inspection methods are slow and only detect surface defects.


## 2. Projective Objectives

The main objectives of this project are as follows:
1. Implementation of Automated Assembly and Disassembly of Battery Cell Winding Processes
To automate the assembly and disassembly of battery cells and winding components using industrial robots, thereby minimizing human error and improving repeatability.
2. Development of a Machine Vision–Based Recognition System
To detect battery cell positions, orientations, and conditions (normal or defective) using camera-based vision systems and AI models, and to integrate the recognition results into the robot control system.
3. Design of Robot Control Logic and State Diagrams
To design structured state diagrams that manage process flow and ensure stable coordination between sensor detection nodes and robotic actions.
4. Verification of Process Reliability and Performance
To experimentally evaluate the success rate, accuracy, and operational stability of the automated system and assess its applicability to real industrial environments.

Process | Target
UR5 Robot Operation | - Bracket detection success rate ≥ 98% - Cell box detection success rate = 100% - Pick and Place success rate ≥ 95% - Stopper linkage success rate = 100% - Assembly/Disassembly process completion time ≤ 1 minute
Indy10 Robot Operation | - Cell orientation detection success rate = 100% - Foreign object detection success rate ≥ 95% - Defective cell detection success rate ≥ 95% - Stopper linkage success rate = 100% - Winding assembly/disassembly process completion time ≤ 1 minute
Defect Detection | - Defect detection success rate (cylindrical surface) ≥ 95% - Defect detection success rate (flat surface) ≥ 80%

## 3. Expected Outcomes

The expected outcomes of this project are as follows:
1. Improved Productivity and Operational Efficiency
By replacing manual labor with robotic automation, continuous operation beyond traditional working hours becomes possible, significantly increasing overall productivity.
2. Enhanced Accuracy and Quality Consistency
The automated system is expected to achieve a high success rate in assembly and disassembly tasks, while the machine vision system enables reliable identification of normal and abnormal battery cells, excluding specific inclusion cases.
3. Reduced Labor Dependency and Improved Workplace Safety
Automating repetitive and potentially hazardous battery handling processes reduces worker exposure to risk and lowers dependence on skilled manual labor.
4. Scalability for Battery Recycling and Future Smart Factory Applications
The proposed system can be extended to battery disassembly and recycling processes, providing a technological foundation for advanced smart factory and sustainable battery production systems.

## 4. Evaluation Index

For each process, 100 iterations of the test are applied to determine the process success rate threshold for each node and set this as the target.

# III. Requirements

## 1. Hardware list

Co-Robot
UR-5e
Indy-10
Grippers
2-finger gripper

Vacuum gripper
Screw-driver
Material

Wind
Cell
Bracket


## 2. Software list

Ubuntu 20.04
Python 3.10.8
Opencv
Numpy

# IV. Procedure

This report covers the camera-based cell and winding disassembly and assembly automation process (UR robot).
disassembly and assembly automation (https://github.com/Joungbin-C/IAIA_Robot_Automation_25-2/tree/main/Report/Report_(Dis)assembly_Automation_Process/Report_(Dis)Assembly_Automation.md)
Process recognition-based pick and place automation (Indy10) and deep learning-based cell defect detection are covered in the following links.

pick and place automation
cell defect detection (https://github.com/shg0873/IAIA/tree/main/Project/Project2_RobotAutomation/Report)

## 1. Overview

The assembly process consists of two main stages: the winding process, and the defective cell detection process. During the winding process, the system identifies the bracket and the empty battery cell. Once the relative coordinates of the windings are detected, the components are assembled. This process also includes a defective cell detection mechanism, which classifies defective products based on flags received during operation.
The disassembly process focuses on removing the windings from the finished battery cell. Like the assembly process, this step also requires the detection of the bracket and the finished battery cell. Once the system detects the relative coordinates of the windings, the components are disassembled and placed into the empty winding box.
The entire process is illustrated in the flow chart below, and the goal of the entire process is to ensure high reliability through rigorous testing. The goal is to perform 100 repeat tests for each process. Based on these tests, a success rate threshold is established for each node, which serves as the target performance standard for the automated system.


You need to run the following nodes in the terminal in order and check the index of each device in the code when connecting the Arduino and camera.

## 2. Detection Node 1: Bracket detecting


The 1st node code is Mid_image_display2. This node determines whether a bracket has arrived. The presence of a bracket is determined by calculating the average intensity value using standard image processing techniques, taking advantage of the fact that the conveyor belt is white and the bracket is black. If the average intensity value falls below the threshold (150.0), a flag is set.

roscore

rosrun indy_driver camera.py

rosrun indy_driver Mid_image_display.py

rosrun indy_driver Mid_image_display2.py

rosrun indy_driver Mid_image_display3.py

rosrun indy_driver Mid_image_display4.py

rosrun indy_driver Mid_image_display5.py

rosrun indy_driver Mid_image_display6.py

rosrun indy_driver Mid_communication.py

roslaunch indy10_moveit_config moveit_planning_execution.launch robot_ip:=192.168.0.8

rosrun indy_driver Mid_project.py

## 3. Detection Node 2: Wind Detecting whether wind combined with cell


The 2nd node code is Mid_image_display4. At this node, the process is determined by determining whether a winder is attached to the cell. If wind is detected through the classical image processing process below, the process proceeds to the disassembly process. If wind is not detected, the process proceeds to the attachment process.


## 4. Detection Node 3: Wind number detection during the composing process


The 3rd node code is Mid_image_display1. This node determines the wind number to be combined during the combination process. Through color detection, if the wind color exceeds a threshold, the box is determined to be filled with wind, and information on which wind number it is is passed to the indy10 robot. Starting from the left, the wind number information is 1, 2, 3 at the top, and 4, 5, 6 at the bottom.


## 5. Detection Node 4: Calculate the wind center During the composing process


The 4th node code is Mid_image_display3. In order to capture the wind to be combined with the cell in the combination process at the corresponding node, the relative coordinates of the wind center are calculated. The relative coordinates are obtained using the formula below after classical image processing, and the return value is the relative coordinates of the wind center [cm].


W denotes word width, H denotes word height
N denotes image pixel width, M denotes image pixel height

## 6. Detection Node 5: Calculating the wind center during the decomposition process


The 5th node code is Mid_image_display5. At this node, the relative coordinates of the wind center are calculated to capture the wind to be separated from the cell during the decomposition process. The relative coordinates are obtained using the following formula after classical image processing, and the return value is the relative coordinates of the wind center [cm]. The formula is the same as for Node 4.


Part | Target | Result | Goal achievement
Detecting part | - Cell orientation detection success rate = 100% | - 100% | O
Pick and Place and Defective Cell Erase | - Foreign object detection success rate ≥ 95% - Defective cell detection success rate ≥ 95% | - 98% - 99% | O
Stopper linkage and process completion time | - Stopper linkage success rate = 100% - Winding assembly/disassembly process completion time ≤ 1 minute | - 100% - Under 57[s] | O

## 7. Detection Node 6: Wind number detection during the decomposition process

The 5th node code is Mid_image_display6. This node determines the number at which to place the disassembled wind during the disassembly process. If the wind color is below a threshold through color detection, the box is determined to be empty and information on the number of the wind is passed to the indy10 robot. The wind numbers are 1, 2, 3 at the top, and 4, 5, 6 at the bottom, starting from the left.

# V. Results

The test was performed a total of 100 times. Process time was measured from the moment the stopper contacts the bracket until the stopper opens at the end of the process.

# VI. Conclusion

This project developed an automated system for the battery cell winding assembly and disassembly process to address the increasing demand for batteries driven by the growth of the electric vehicle market and to address the productivity and safety issues inherent in existing manual processes. By integrating industrial robots and machine vision technology, we implemented an intelligent process that performs bracket and cell detection, defect detection, assembly, and disassembly. The system's reliability was verified through 100 repeated experiments. The results showed a 100% success rate in cell orientation detection and stopper linkage, and a 98% or higher success rate in foreign matter and defective cell detection, exceeding the targets in all evaluation indicators. Notably, by shortening the process completion time to less than 57 seconds, well below the target of one minute, this system proved to be an effective solution that can dramatically improve production efficiency and work safety in the battery manufacturing and recycling industries.

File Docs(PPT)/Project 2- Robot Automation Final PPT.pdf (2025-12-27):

# Battery Cell Winding Process

Industrial | AI | & | Automation

2025.12.05

22000355 HyeonGyu Seo / 22000167 Inyeop Kim / 22200757 Joungbin Choi

Prof. Young-Keun Kim
School of Mechanical & Control Engineering Handong Global University

### 1. Background

1-1) 배터리 시장 현황
1-2) 문제점
1-3) 목표

### 2. Robot AI Process

2-1) Material
2-2) 조립 공정
2-3) 분해 공정

### 3. 공정 인식 기반 Pick and Place 자동화

3-1) Process
3-2) 목표
3-3) State Diagram
3-4) 감지 노드
3-5) 결과
3-6) 문제점 분석

## Contents

### 4. 카메라 인식 기반 Cell & Wind 분해 및 결합 자동화

4-1) Process & Target
4-2) 목표
4-3) State Diagram
4-4) 감지 노드
4-5) 결과
4-6) 문제점 분석

### 5. Detecting Defect

5-1) 목적 및 개요
5-2) 원형 검사
5-3) 원형 검사 목표 및 결과
5-4) 표면 검출
5-5) 표면 검출 모델
5-6) 표면 검출 목표 및 결과
5-7) Cell Logic

### 6. Conclusion

## 1. Background

1-1. 배터리 시장 현황

- 2030년에는 전기차 비중이 40%를 넘어설 것으로 보이며, 2차전지 시장은 약 3700억
달러까지 성장할 전망
- 중국은 자국 경쟁력 확보로 세계 점유율의
65% 수준까지 주도권 확보
- 한국의 기술력도 강하지만 여전히 R&D, 재 활용 체계 구축은 주요 과제(특히 재활용 체
계 구축을 위해서는 조립 공정 뿐만 아니라
분해 공정도 중요)


Figure 1. 배터리 시장 현황

## 1. Background

1-2. 문제점

- 미세 공정 편차는 잠재 결함을 만들고, 이는 배터리 고장 및 안전사고로 이어짐
- 대량 생산에서는 공정 변동이 커 균일성 확
보 문제 발생
- 기존의 불량 검사 방식은 느리고 표면만 검
출된다는 문제점 존재


Figure 2. 조립 공정 결함 유형

## 1. Background

- 불량률을 줄이기 위해 공정 편차를 최소화하면서도 빠른 공정이 필요(카메라 기반 탐지 / 공정 프로세스 사이클은 3분 이내 완료로 목표)
- UR5e 로봇은 스스로 조립 / 분해 공정을 파악한 후 각 공정에 맞게 셀 Pick and Place 수행
- Detecting Defect 파트는 불량 셀을 감지하고 결과를 Indy10에 정확하게 전송
- Indy10 로봇은 와인딩 조립 / 분해 및 불량 셀 소거

1-3. 목표

## 1. Background

1-3. 목표

| 공정 | 목표
공정 인식 기반 Pick and Place 자동화 | | - 브라켓 감지 성공률 ≥ 98% - 셀 박스 감지 성공률 = 100% - Pick and Place 성공률 ≥ 95% - Stopper 연동 성공률 = 100% - 조립 / 분해 공정 완료 시간: 1분 이내
Indy10 | | - 셀 / 와인딩 감지 성공률 = 100% - 와인딩 조립 / 분해 성공률 ≥ 95% - 불량 셀 소거 성공률 ≥ 95% - Stopper 연동 성공률 = 100% - 와인딩 조립 / 공정 완료 시간: 1분 이내
Detecting Defect | | - 불량 셀 감지 성공률(원형) ≥ 95% - 불량 셀 감지 성공률(표면) ≥ 80%

## 2. Robot AI Process

<Wind> | <Cell> | <Bracket> | <Composite>

2-1. Material

## 2. Robot AI Process

UR Robot; Indy10 Robot; Camera; Ultrasonic Sensor; Stopper; Cell; Composite; Wind

## 2. Robot AI Process

UR Robot; Indy10 Robot; Camera; Ultrasonic Sensor; Stopper; Cell; Composite; Wind

## 2. Robot AI Process

Check for Defect

## 2. Robot AI Process

UR Robot; Indy10 Robot; Camera; Stopper; Ultrasonic Sensor; Cell; Composite; Wind

## 2. Robot AI Process

UR Robot; Indy10 Robot; Camera; Stopper; Ultrasonic Sensor; Cell; Composite; Wind

## 2. Robot AI Process

UR Robot; Indy10 Robot; Camera; Stopper; Ultrasonic Sensor; Cell; Composite; Wind

## 2. Robot AI Process

## 2. Robot AI Process

UR Robot; Indy10 Robot; Camera; Stopper; Ultrasonic Sensor; Cell; Composite; Wind

## 2. Robot AI Process

UR Robot; Indy10 Robot; Camera; Stopper; Ultrasonic Sensor; Cell; Composite; Wind

## 2. Robot AI Process

UR Robot; Indy10 Robot; Camera; Stopper; Ultrasonic Sensor; Cell; Composite; Wind

## 2. Robot AI Process

UR Robot; Indy10 Robot; Camera; Stopper; Ultrasonic Sensor; Cell; Composite; Wind

## 2. Robot AI Process

## 2. Robot AI Process

UR Robot; Indy10 Robot; Camera; Stopper; Ultrasonic Sensor; Cell; Composite; Wind

## 2. Robot AI Process

UR Robot; Indy10 Robot; Camera; Stopper; Ultrasonic Sensor; Cell; Composite; Wind

## 3. 공정 인식 기반 Pick and Place 자동화

3-1) Process

A. 조립 공정
1. 빈 셀
- 빈 셀을 셀 박스에서 감지 및 Pick(상대좌표로 감지
및 Pick)
- 브라켓 감지
- 브라켓에 Place(상대좌표로 Place)
2. 완성된 셀
- 브라켓에 있는 완성된 셀 감지 및 Pick(상대좌표로
감지 및 Pick)
- 셀 박스 감지
- 셀 박스에 Place(절대좌표로 진행)
B. 분해 공정
1. 완성된 셀
- 완성된 셀을 셀 박스에서 감지 및 Pick(상대좌표로
감지 및 Pick)
- 브라켓 감지
- 브라켓에 Place(상대좌표로 Place)
2. 빈 셀
- 브라켓에 있는 빈 셀 감지 및 Pick(상대좌표로 감지
및 Pick)
- 셀 박스 감지
- 셀 박스에 Place(절대좌표로 진행)

3-2) 목표

파트 | 목표
감지 부분 | - 브라켓 감지 성공률 ≥ 98% - 셀 박스 감지 성공률 = 100%
Pick and Place | - Pick and Place 성공률 ≥ 95%
Stopper 연동 및 공정 완료 시간 | - Stopper 연동 성공률 = 100% - 조립 / 분해 공정 완료 시간: 1분 이내

## 3. 공정 인식 기반 Pick and Place 자동화

## 3. 공정 인식 기반 Pick and Place 자동화

3-3) State Diagram; Start; 완성된 셀과 브라켓을 감지하는가?; 완성품 셀 Pick and Place; 빈 셀 박스로 이동; 브라켓; 완성된 셀 감지 시; 빈 셀 Pick and Place Stopper Open; 빈 셀을 감지하는가?; Yes; 빈 셀과 브라켓을 감지 하는가?; 빈 셀 Pick and Place; 완성품 박스로 이동; 브라켓 감지 시; 완성품 셀 Pick and Place Stopper Open; 완성품 셀을 감지하는 가?

--- State의 감지 조건은 감지 노드를 통해 모두 처리함 ------Ultrasonic Sensor에서 브라켓을 감지하면 Stopper가 닫히는 과정은 아두이노에서 자체 구현---

## 3. 공정 인식 기반 Pick and Place 자동화


3-4) 감지 노드

A) Bracket

<Color Detecting: RGB>; <inRange>; <Find Center>; 원형 중심점 감지 및 카메라 중심점 기반 이동 거리 계산(Output); 원 중심점; 카메라 중심점; 이동해야 할 거리 (Ex: x축=83.5mm, y축=7.3mm)

- 브라켓 위치를 정확히 감지해서 셀을 브라켓 안에 Place 하기 위한 감지

RGB로 색 감지(Input) -> InRange로 임계값 기반 Masking(Input) ->

## 3. 공정 인식 기반 Pick and Place 자동화

3-4) 감지 노드

B) Cell Box

<RGB: Gray > 0.25>
셀이 있는 박스가 감지되서
Pick 수행


<RGB: Black > 0.75>
셀이 없는 박스가 감지되서
Place 수행
- 셀이 있는 박스와 없는 박스를 구별해서 Pick, Place를 수행하기 위한 감지

RGB로 색 감지(Input) -> 특정 색상이 일정 비율 이상 / 이하이면 감지 활성화(Output)

감지됨

감지 안됨

감지 안됨

감지됨

## 3. 공정 인식 기반 Pick and Place 자동화

3-4) 감지 노드

C) Composite Box

<RGB: Orange > 0.25>
셀이 있는 박스가 감지되서
Pick 수행

<Thresholding < 110>
셀이 없는 박스가 감지되서
Place 수행
- 셀이 있는 박스와 없는 박스를 구별해서 Pick, Place를 수행하기 위한 감지
1) RGB로 색 감지(Input) -> 주황색이 일정 비율 이상이면 감지 활성화(Output)
2) Threshold로 감지(Input) -> 픽셀 밝기 임계값이 110 이하이면 감지 활성화(Output)

감지됨

감지 안됨

감지됨

감지 안됨

## 3. 공정 인식 기반 Pick and Place 자동화

3-4) 감지 노드

D) Cell

<Canny Edge>

<Find Center>

- 셀 종류(Cell, Composite)를 정확히 감지해서 공정에 맞게 셀을 Pick and Place 하기 위한 감지
1) 빈 셀: Canny Edge로 경계선 감지(Input) → 원 형 중심점 감지 및 카메라 중심점 기반 이동 거리 계산(Output)
2) Composite 셀: Canny Edge로 경계선 AND RGB 로 Composite 셀 감지(Input) → 원형 중심점 감지 및 카메라 중심점 기반 이동 거리 계산 (Output)

## 3. 공정 인식 기반 Pick and Place 자동화

3-4) 감지 노드

D) Cell

<Color Detecting: RGB>

<Find Center>

<Canny Edge>

- 셀 종류(Cell, Composite)를 정확히 감지해서 공정에 맞게 셀을 Pick and Place 하기 위한 감지
1) 빈 셀: Canny Edge로 경계선 감지(Input) → 원 형 중심점 감지 및 카메라 중심점 기반 이동 거리 계산(Output)
2) Composite 셀: Canny Edge로 경계선 AND RGB 로 Composite 셀 감지(Input) → 원형 중심점 감지 및 카메라 중심점 기반 이동 거리 계산 (Output)

3-5) 결과

파트 | 목표 | 결과
감지 부분 | - 브라켓 감지 성공률 ≥ 98% - 셀 박스 감지 성공률 = 100% | - 브라켓 감지 성공률 = 100% - 셀 박스 감지 성공률 = 100%
Pick and Place | - Pick and Place 성공률 ≥ 95% | - Pick and Place 성공률 = 97%
Stopper 연동 및 공정 완료 시간 | - Stopper 연동 성공률 = 100% - 조립 / 분해 공정 완료 시간: 1분 이내 | - Stopper 연동 성공률 = 100% - 조립 / 분해 공정 완료 시간: 1분 35초

## 3. 공정 인식 기반 Pick and Place 자동화

- Test는 총 100회 시행
- 공정 시간은 Stopper가 브라켓에 닿는 순간부터 프로세스 완료 후 Stopper가 열리는 시점까지로 측정

3-5) 결과(평가)

파트 | 결과 | 평가
감지 부분 | - 브라켓 감지 성공률 = 100% - 셀 박스 감지 성공률 = 100% | - 감지는 모두 100%로 완벽히 성공
Pick and Place | - Pick and Place 성공률 = 97% | - Pick and Place 성공률은 목표치를 달성 했으나 100회 중 3회 실패했기 때문에 분 석 필요
Stopper 연동 및 공정 완료 시간 | - Stopper 연동 성공률 = 100% - 조립 / 분해 공정 완료 시간: 1분 35초 | - Stopper 연동 성공률 = 100%를 달성했 으나 조립 / 분해 공정 시간이 목표로 삼 았던 1분보다 더 오래 걸렸기 때문에 분 석 필요

## 3. 공정 인식 기반 Pick and Place 자동화

- Pick and Place는 목표치 ≥ 95%를 달성했지만, 배터리 셀 조립 / 분해 공정에서 실패는 중요한 문제이 기 때문에 분석 필요
- 분해 / 공정 목표 시간 달성 실패한 부분에 대해 분석 필요(목표치: 1분 이내)

## 3. 공정 인식 기반 Pick and Place 자동화

3-6) 문제점 분석

- Pick and Place 100회 실행 결과 3회 실패

상대좌표 함수
→ go_to_joint_rel()의 tolerance는 0.003, 즉 최대 3mm까지 허용됨
→ 단 tolerance 값을 너무 작게 할 경우, 경로 계산 시간 증가(Trade off) → Trade off를 고려해서 tolerance 값을 더 세밀하게 조절해야 함
- 느린 조립 / 분해 공정

→ 로봇의 공간좌표 X, Y, Z를 직접 지정하여 이동시키는 카르테시안 기법은 자세(yaw/pitch/roll) 의 부호 반전 위험이 없고 또한 경로 계산을 2mm마다 하도록 나누었기 때문에 정밀하지만 움직임 느림
→ 기존의 end-effector의 자세(yaw/pitch/roll)를 통해 움직임을 제어할 경우(Euler 기법) 속도는 빠 르지만 간혹 자세 부호가 반전될 때 로봇이 틀어지는 심각한 문제 발생(Trade off)
→ 감지 노드를 콜백할 때 딜레이 시간 존재(측정 결과 약 1.5s이며, rospy.sleep() 문제보다는 ROS 통신 자체의 문제

4-1) Process & Target

A. 조립 공정
1. 와인딩 공정
- 브라켓 감지
- 빈 배터리 셀 감지
- 와인드 상대좌표 감지후 결합
2. 불량셀 감지
- 수신 받은 플래그 기반 불량품 구분
B. 분해 공정
1. 완성된 배터리 셀에서 와인드 분해 공정
- 브라켓 감지
- 완성품 배터리 셀 감지
- 와인드 상재좌표 감지후 분해 및 빈 와인드 박스에 위치
C. 공정 목표

각 공정 프로세스 별로 100 번의 반복 테스트를 적용하여 각 노드 별로 공정 성공률 임계치를 정하고 이를 목표로 한다.

## 4. 카메라 인식 기반 Cell & Wind 분해 및 결합 자동화

4-2) 목표

파트 | 목표
Detecting 부분 | - 셀 / 와인딩 감지 성공률 = 100%
Pick and Place 및 불량 셀 소거 | - 와인딩 조립 / 분해 성공률 ≥ 95% - 불량 셀 소거 성공률 ≥ 95%
Stopper 연동 및 공정 완료 시간 | - Stopper 연동 성공률 = 100% - 조립 / 분해 공정 평균 완료 시간: 1분 이하

## 4. 카메라 인식 기반 Cell & Wind 분해 및 결합 자동화

## 4. 카메라 인식 기반 Cell & Wind 분해 및 결합 자동화

Start; Detect 2; Compose mode; Decompose mode; Bracket Arrive; Detect 1; Mid_communication; Detect 3; Detect 6; wind num; Detect 4; Detect 5; wind pose; Pick & Place; 4-3) State Diagram; Yes; Wind 검출; Wind 미 검

wind num cell state
flag

4-4) 감지 노드1: Bracket 감지

해당 노드에서 Bracket의 도착 여부를 판별한다.

Bracket의 도착 여부는 컨베이어 벨트가 하얀색 Bracket이 검은색임을 활용해 고전영상처리로 평균 intensity 값을 계산하며 임계값(150.0) 이하 일 때 플래그가 넘어간다.

Average Intensity : 89.51

## 4. 카메라 인식 기반 Cell & Wind 분해 및 결합 자동화

4-4) 감지 노드2: Wind 결합 여부 감지

해당 노드에서는 cell에 winder의 결합 여부를 판단하여 진행 공정을 결정한다.

아래와 같은 고전영상처리 프로세스를 통해 wind가 감지 되었을 경우 분해공정으로, 감지되지 않았을 경우 결합공정으로 넘어가게 된다.

<CvtColoar HSV> | <inRange>
주황색 색상 검
출

<Morphology: Open>
Mask 생성

<FindContour>
윤곽선 검출로
Wind 존재 유무 감
지

## 4. 카메라 인식 기반 Cell & Wind 분해 및 결합 자동화

4-4) 감지 노드3: 결합 공정 시 Wind 번호 감 지
해당 노드에서는 결합 공정 시 결합할 wind 번호를 결정한다.

색상 검출을 통해 wind 색이 임계값을 이상일 경우 박스에 wind가 채워져 있는 것으로 판단하며 몇 번째 wind인지에 대한 정보를 indy10 로봇에게 넘긴다.
왼쪽부터 상단에서 1,2,3 하단에서 4,5,6의 wind number 정보를 가진다.

Wind is in num2 and num6

## 4. 카메라 인식 기반 Cell & Wind 분해 및 결합 자동화


## 4. 카메라 인식 기반 Cell & Wind 분해 및 결합 자동화

4-4) 감지 노드4: 결합 공정 시 Wind 중심 상대 좌표 계산
해당 노드에서 결합공정에서 cell에 결합할 wind를 잡기 위해 wind 중 심의 상대좌표를 계산한다. 상대좌표는 고전영상처리 이후 아래 수식

으로 구해지며 반환 값은 wind 중심의 상대 좌표 [cm].

xcm = − v −

M
2

⋅

M
H

ycm = − u −

N
2

⋅

N
W
- W denotes Word Width
- H denotes Word Height
- N denotes Image pixel width
- M denotes Image pixel height

4-4) 감지 노드5: 분해 공정 시 Wind 중심 상대 좌표 계산
해당 노드에서 분해공정에서 cell에서 분리할 wind를 잡기 위해 wind 중심의 상대좌표를 계산한다. 상대좌표는 고전영상처리 이후 아래 수 식으로 구해지며 반환 값은 wind 중심의 상대 좌표 [cm].

## 4. 카메라 인식 기반 Cell & Wind 분해 및 결합 자동화

4-4) 감지 노드6: 분해 공정 시 Wind 번호 감 지
해당 노드에서는 분해 공정시 분해한 wind를 놓을 번호를 결정한다.

색상 검출을 통해 wind 색이 임계값 이하일 경우 박스에 wind가 비어 있는 것으로 판단하며 몇 번째 wind인지에 대한 정보를 indy10 로봇에게 넘긴다.
왼쪽부터 상단에서 1,2,3 하단에서 4,5,6의 wind number 정보를 가진다.

Wind is in num2 and num6

## 4. 카메라 인식 기반 Cell & Wind 분해 및 결합 자동화

4-5) 결과

파트 | 목표 | 결과
Detecting 부분 | - 셀 / 와인딩 감지 성공률 = 100% | - 셀 / 와인딩 감지 성공률 = 100%
Pick and Place 및 불량 셀 소거 | - 와인딩 조립 / 분해 성공률 ≥ 95% - 불량 셀 소거 성공률 ≥ 95% | - 와인딩 조립 / 분해 성공률 = 98% - 불량 셀 소거 성공률 = 99%
Stopper 연동 및 공정 완료 시간 | - Stopper 연동 성공률 = 100% - 조립 / 분해 공정 완료 시간: 1분 이내 | - Stopper 연동 성공률 = 100% - 조립 / 분해 공정 평균 완료 시간: 57s
- Test는 총 100회 시행
- 공정 시간은 Stopper가 브라켓에 닿는 순간부터 프로세스 완료 후 Stopper가 열리는 시점까지로 측정

## 4. 카메라 인식 기반 Cell & Wind 분해 및 결합 자동화

4-5) 결과 평가

파트 | 결과 | 평가
Detecting 부분 | - 셀 / 와인딩 감지 성공률 = 100% | - 감지는 모두 100%로 완벽히 성공
Pick and Place 및 불량 셀 소거 | - 와인딩 조립 / 분해 성공률 = 98% - 불량 셀 소거 성공률 = 99% | - Pick and Place 성공률은 목표치를 달성 했으나 100회 중 2회 실패에 대한 분석 필요
Stopper 연동 및 공정 완료 시간 | - Stopper 연동 성공률 = 100% - 조립 / 분해 공정 평균 완료 시간: 57s | - Stopper 연동 성공률 = 100%를 달성했 으나 조립 / 분해 공정 시간이 목표로 삼 았던 1분은 평균 완료 시간은 충족하였으 나 1분을 초과하는 경우에 대한 분석 필 요
- Pick and Place는 목표치 ≥ 95%를 달성했지만, 배터리 셀 조립 / 분해 공정에서 실패는 중요한 문제이 기 때문에 분석 필요
- 분해 / 공정 목표 시간 달성 실패한 부분에 대해 분석 필요(목표치: 1분 이내)

## 4. 카메라 인식 기반 Cell & Wind 분해 및 결합 자동화

4-6) 문제점 분석

- Pick and Place 100회 실행 결과 cell/wind 인식 확률 100%, 상대 좌표 부정확도로 인한 결합 2회 실패

상대좌표 함수
→ go_to_joint_rel()의 tolerance는 0.003, 즉 최대 3mm까지 허용됨
→ 단 tolerance 값을 너무 작게 할 경우, 로봇의 경로 계산 시간 증가(Trade off)
→ Trade off를 고려해서 tolerance 값을 더 세밀하게 조절해야 함
- 느린 조립 / 분해 공정

→ 감지 노드를 콜백할 때 딜레이 시간 존재(측정 결과 약 1.5s이며, rospy.sleep() 문제보다는 ROS 통신 자체의 문제
→ 각 프로세스 종료 시마다 ros 노드를 초기화하여 딜레이 시간을 최소화하는 방법을 사용해서 목표로 삼았던 공정 완료 시간 (1분)을 충족한다.

## 4. 카메라 인식 기반 Cell & Wind 분해 및 결합 자동화

## 5. Detecting Defect

## 결함 케이스:

## 1. 윗면에 Circularity Check

2. 옆면에 결함(inclusion,

## pitted, rugged, scratch)

# 5-1. 목적 및 개요 : 배터리 셀의 결함을 확인하고 정상인 비

정상인지 판별하여 로봇에게 flag를 전송한다.


Upper Circle Check | Surface Detection

## 5. Detecting Defect

## 5-1. 목적 및 개요

No

No

Yes

Yes

## 5. Detecting Defect

### 5-2. 원형 검사

1. Extract center ROI (1000X1000)
2. Convert to grayscale
3. Apply Gaussian blur
4. Detect outer circle using Hought Circle
5. Validate radius/area
6. Create a ring-shaped mask using outer radius (25pixel)
7. Apply Canny edge detection and extract contours

## 5. Detecting Defect

Grayscale | Gaussian blur | Hough Circle

5-2. 원형 검사

## 5. Detecting Defect

Ring Mask | Ring ROI | Canny Edge

5-2. 원형 검사

## 5. Detecting Defect


Contour | Result

5-2. 원형 검사

## 5. Detecting Defect

## 5-3. 원형 검사 결과

1. Compute circularity of largest

contour

1. Circularity = 4πA/P

2

2. Circularity≥0.85 → Crack
3. Accuracy :
- Cell Okay :

102/105 * 100 = 97.14 %

- Cell Not Okay :

100/105 * 100 = 95.24 %

| 목표 [%] | 결과 [%]
Cell Okay | ≥95 | 97.14
Cell Not Okay | ≥95 | 95.24

## 5. Detecting Defect

## 5-4. 표면 검출

1. Detecting Surface Defect
2. Detects surface scratches,

dents, and other defects

## 5. Detecting Defect

## 5-5. 표면 검출 모델

1. Train
1. Windows, Python 3.10, YOLOv8s.pt
2. Epoch: 100
3. Batch: 8
4. Optimizer AdamW(lr=0.001)
5. Early Stop : 20
6. Final : Epoch = 53
7. Class : pitted, rugged, scratch
8. Total Train Dataset : 1314
1. 400, 552, 346, 403

## 5. Detecting Defect


Scratch | Rugged | Pitted | Inclusion

## 5. Detecting Defect

## 5-5. 표면 검출 모델

## 5. Detecting Defect

## 5-6. 표면 검출 결과

Out of 50 trial

| 목표 [%] | 결과 [%]
Inclusion | ≥80 | 24/50 = 48
Pitted | ≥80 | 47/50 = 94
Rugged | ≥80 | 43/50 = 86
Scratch | ≥80 | 43/50 = 86

## 5. Detecting Defect

## 5-7. 문제 분석

Inclusion은 있으면 안되는 물질이 포함되었을 때이다.

## - 현재 테스트에서 사용되는 셀은 실제 배터리와 사용

## 되는 물질이 다르고 inclusion이라 classify할 수 있는

부분이 모호하다.

## - 다음 사진과 같은 길고 가느다란 선은 YOLO모델이

예측하기에는 어려운 feature이다.

## 5. Detecting Defect

5-8. Cell Logic

1. Send the flag depends on the

result of detected cells

2. Cell 2 Timeout (10 frames)
Cell1 | Cell2 | Final Flag
OK | OK | 1
NOK | OK | 2
OK | NOK | 3
NOK | NOK | 4
OK | None | 5
NOK | None | 6

Not Okay Cases

Table) Flag Logic

6. Conclusion | 파트 | 목표 | 결과
Detecting 부분 | - 셀 / 와인딩 감지 성공률 = 100% | - 셀 / 와인딩 감지 성공률 = 100%
Pick and Place 및 불량 셀 소거 | - 와인딩 조립 / 분해 성공 률 ≥ 95% - 불량 셀 소거 성공률 ≥ 95% | - 와인딩 조립 / 분해 성공 률 = 98% - 불량 셀 소거 성공률 = 99%
Stopper 연동 및 공정 완 료 시간 | - Stopper 연동 성공률 = 100% - 조립 / 분해 공정 완료 시간: 1분 이내 | - Stopper 연동 성공률 = 100% - 조립 / 분해 공정 평균 완료 시간: 57s
파트 | 목표 | 결과
감지 부분 | - 브라켓 감지 성공률 ≥ 98% - 셀 박스 감지 성공률 = 100% | - 브라켓 감지 성공률 = 100% - 셀 박스 감지 성공률 = 100%
Pick and Place | - Pick and Place 성공률 ≥ 95% | - Pick and Place 성공률 = 97%
Stopper 연동 및 공정 완 료 시간 | - Stopper 연동 성공률 = 100% - 조립 / 분해 공정 완료 시간: 1분 이내 | - Stopper 연동 성공률 = 100% - 조립 / 분해 공정 완료 시간: 1분 35초

## - 로봇 공정

## - 목표치 보다 높은 성공률

## 로 정확하고 빠른 조립 및

## 분해 공정 가능

## 6. Conclusion

| 목표 [%] | 결과 [%]
Inclusion | ≥80 | 24/50 = 48
Pitted | ≥80 | 47/50 = 94
Rugged | ≥80 | 43/50 = 86
Scratch | ≥80 | 43/50 = 86
| 목표 [%] | 결과 [%]
Cell Okay | ≥95 | 97.14
Cell Not Okay | ≥95 | 95.24

## - 머신 비전 검출

## - Inclusion을 제외한 모든 부분

## 에서 셀의 정상과 비정상 상태

## 를 구분 가능

## 6. Conclusion

## - 자동화를 통한 기대 효과

- 시간 | : 인력 : 1일 8시간 주5일 근무 -> 로봇 : 1일 24시간 주7일 근무
- 사이클 타임 | : 인력 : 2셀 기준 10 초 -> 로봇 : 2셀 기준 약 1분
- 검출 | : 인력 : 약 70~90% 정확성 (Jo, H) -> 머신 비전 : 약 92% 정확성
- 검색 속도 : 머신 비전이 검색 속도(search speed) 120% 빠르다(Jiang, X)
- 결론
- 인력과 재정을 아끼며 높은 정확성으로 공장 효율을 높일 수 있다.

### - Future Study

- 공정 속도를 높이고 surface detection 정확성 향상

## Reference

1. 박예나. (2024년 11월 17일). “배터리 삼국지”… 中 질주 속 K배터리의 난제는. 서울경제. https://www.sedaily.com/NewsView/29X4QWC74S
2. Attia, P. M., Moch, E., & Herring, P. K. (2025). Challenges and opportunities for high-quality battery production at scale. Nature Communications, 16, 611. https://doi.org/10.1038/s41467-025-55861-7
3. Jiang, X., Gramopadhye, A.K., Melloy, B.J. and Grimes, L.W. (2003), Evaluation of best system performance: Human, automated, and hybrid inspection systems. Hum. Factors Man., 13: 137-152. https://doi.org/10.1002/hfm.10031
4. Jo, H., Park, H., Baek, S., & Kang, E. K. (2017). Low back pain in farmers: The association with agricultural work management, disability, and quality of life in Korean farmers. Human Factors and Ergonomics in Manufacturing & Service Industries, 27(3), 156–165. https://doi.org/10.1002/hfm.20699

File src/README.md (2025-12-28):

# Program Guideline

**Date:** 2025/12/27

**Author:** Joungbin Choi, Hyeongyu Seo, Inyeop Kim

**본 문서는 Robot Automation Project 보고서의 명령어 매뉴얼 부분을 한국어로 작성한 것이다.**

## 파일 구조

```
catkin_ws
  |- build
  |- devel
  |- src
  |----|- CMakeLists.txt
  |----|- 22000167_Kiminyeop_ur_python
  |----|----|- CMakeLists.txt
  |----|----|- package.xml
  |----|----|- msg
  |----|----|----| grip_command.msg
  |----|----|----| grip_state.msg
  |----|----|----| object_info.msg
  |----|----|----| pet_info.msg
  |----|----|----| robot_state.msg
  |----|----|- src
  |----|----|----| camera.py
  |----|----|----| cell_detection.py
  |----|----|----| composite_detection.py
  |----|----|----| empty_cell_box_detection_node.py
  |----|----|----| empty_composite_cellbox_detection_node.py
  |----|----|----| filled_cellbox_detection_node.py
  |----|----|----| filled_composite_cellbox_detection_node.py
  |----|----|----| main.py
  |----|----|----| move_group_python_interface.py	
  |----|----|----| winding_detect_node.py	
  |----|----|----| yellow_bracket_detection_node.py
  |----|- indy_driver
  |----|----|- msg
  |----|----|----|- comp_wind_info.msg
  |----|----|----|- decomp_wind_info.msg
  |----|----|----|- bracket_info.msg
  |----|----|----|- comp_pose_info.msg
  |----|----|----|- decomp_pose_info.msg
  |----|----|----|- cell_state_info.msg
  |----|----|----|- process_info.msg
  |----|----|- src
  |----|----|----|- camera.py
  |----|----|----|- Mid_image_display.py
  |----|----|----|- Mid_image_display2.py
  |----|----|----|- Mid_image_display3.py
  |----|----|----|- Mid_image_display4.py
  |----|----|----|- Mid_image_display5.py
  |----|----|----|- Mid_image_display6.py
  |----|----|----|- Mid_communication.py
  |----|----|----|- Mid_project.py
  |----|----|----|- CmakeLists.txt
  |----|----|----|- package.yml
  |----|- MachineVision
  |----|----|- AcquireAndDisplay_Final.py
  |----|----|- best.pt
  |----|----|- train
  |----|----|----|- ...
```

## 소프트웨어 설정

- OS: Linux Ubuntu 20.04

- ROS: ROS Noetic

- Virtual Environment: Anaconda

  - Machine Vision 용 가상환경 생성 및 설정은 [링크](https://github.com/Joungbin-C/IAIA_Robot_Automation_25-2/blob/main/src/MachineVision/README.md)를 따른다
    - ```bash
      conda create -n pyspin python=3.10 -y
      conda activate pyspin
      python -m ensurepip
      python -m pip install --upgrade pip
      
      # 설치한 버전으로 변경
      cd C:\path\to\spinnaker_python_wheel
      pip install spinnaker_python-3.x.x.x-cp38-cp38-linux_x86_64.whl 
      
      pip install numpy==2.2.6
      pip install opencv-python-headless==4.10.0.84
      pip install ultralytics==8.3.232
      pip install PyQt5==5.15.11
      pip install Pillow==9.2.0
      ```
- Additional Ubuntu utility programs

  - terminator
  - Visual Code

추가적인 소프트웨어 설정은 [링크](https://github.com/hyKangHGU/Industrial-AI-Automation_HGU/tree/main/tutorial/ubuntu)를 따른다.

## Terminal 명령어 모음

#### UR5e 실행

우선 UR5e 로봇을 실행 전 my_robot_calibration.yaml을 홈 파일에 저장한 후 다음과 같은 명령어를 터미널에 실행한다.
```
chmod+x/~my_robot_calibration.yaml
```

그리고 아래 노드를 순서대로 실행한다.
```
cd~/catkin_ws
catkin_make
roscore

roslaunch ur_robot_driver ur5e_bringup.launch robot_ip:=192.168.0.2

roslaunch ur5e_rg2_moveit_config move_group.launch

chmod +x ~/catkin_ws/src/ur_python/src/camera.py
rosrun 22000167_Kiminyeop_ur_python camera.py

chmod +x ~/catkin_ws/src/ur_python/src/yellow_bracket_detection_node.py
rosrun 22000167_Kiminyeop_ur_python yellow_bracket_detection_node.py

chmod +x ~/catkin_ws/src/ur_python/src/filled_cellbox_detection_node.py
rosrun 22000167_Kiminyeop_ur_python filled_cellbox_detection_node.py

chmod +x ~/catkin_ws/src/ur_python/src/empty_composite_cellbox_detection_node.py
rosrun 22000167_Kiminyeop_ur_python empty_composite_cellbox_detection_node.py

chmod +x ~/catkin_ws/src/ur_python/src/filled_composite_cellbox_detection_node.py
rosrun 22000167_Kiminyeop_ur_python filled_composite_cellbox_detection_node.py

chmod +x ~/catkin_ws/src/ur_python/src/empty_cell_cellbox_detection_node.py
rosrun 22000167_Kiminyeop_ur_python empty_cell_cellbox_detection_node.py

chmod +x ~/catkin_ws/src/ur_python/src/winding_detect_node.py
rosrun 22000167_Kiminyeop_ur_python winding_detect_node.py

chmod +x ~/catkin_ws/src/ur_python/src/composite_detection.py
rosrun 22000167_Kiminyeop_ur_python composite_detection.py

chmod +x ~/catkin_ws/src/ur_python/src/cell_detection.py
rosrun 22000167_Kiminyeop_ur_python cell_detection.py
```

**아두이노 실행은 아래와 같은 절차를 따른다.**
Arduino 1.8.19를 설치한 후, 상단 도구 모음에서 보드가 **Arduino Uno**로 설정되어 있고 포트가 **/dev/tty/ACM0**인지 확인한다.  
설정을 확인한 뒤 업로드를 진행하고, 업로드가 완료되면 Arduino 창을 닫는다.

**마지막으로 VS code에  들어가서 main.py를 실행한다.**

#### Indy10 실행

아두이노와 카메라를 연결할 때는 터미널에서 다음 노드들을 순서대로 실행하고, 코드(camera.py, Mid_project.py)에서 각 장치의 인덱스를 확인한다.
```bash
roscore

rosrun indy_driver camera.py

rosrun indy_driver Mid_image_display.py

rosrun indy_driver Mid_image_display2.py

rosrun indy_driver Mid_image_display3.py

rosrun indy_driver Mid_image_display4.py

rosrun indy_driver Mid_image_display5.py

rosrun indy_driver Mid_image_display6.py

rosrun indy_driver Mid_communication.py

roslaunch indy10_moveit_config moveit_planning_execution.launch robot_ip:=192.168.0.8
rosrun indy_driver Mid_project.py
```

#### Machine Vision 실행

```bash
conda activate pyspin
cd ~/catkin_ws/MachineVision/AcquireAndDisplay_Final.py
python AcquireAndDisplay_Final.py
```

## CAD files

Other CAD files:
Hardware/base_plate.dwg
Hardware/Profile_Holder.ipt
Hardware/Profile_Plate_Holder.ipt
Hardware/USB_camera.ipt
Hardware/base_plate.ipt
Hardware/bracket_1.ipt
Hardware/bracket_2.ipt
Hardware/camera_post.ipt
Hardware/camera_robotarm.ipt
Hardware/camera_robotarm2.ipt
Hardware/cell.ipt
Hardware/cell_braket.ipt
Hardware/motor_limit_1.ipt
Hardware/motor_limit_2.ipt
Hardware/post.ipt
Hardware/post_bottom.ipt
Hardware/sonic_sensor_holder.ipt

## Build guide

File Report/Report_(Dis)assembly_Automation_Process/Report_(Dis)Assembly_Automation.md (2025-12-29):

# Project: Assembly/Disassembly_Automation
---
Industrial AI & Automation 2025

**Name:** Inyeop Kim

**Date:** 2025/12/27

**github link**
https://github.com/Joungbin-C/IAIA_Robot_Automation_25-2

**Demo link**
[IAIA Robot Automation](https://www.youtube.com/watch?v=vMVNzXjdA7o)
## I. Introduction
---
With the rapid growth of the electric vehicle (EV) market, the secondary battery industry has emerged as a key strategic sector. It is projected that by 2030, electric vehicles will account for more than 40% of the global automotive market, leading to a significant increase in battery production demand. However, conventional battery cell assembly and disassembly processes remain highly dependent on manual labor, resulting in limitations in productivity, process consistency, and quality control. In particular, as the importance of battery recycling and safe disassembly increases, there is a growing demand for intelligent automation systems capable of handling precise and complex operations beyond simple assembly tasks.

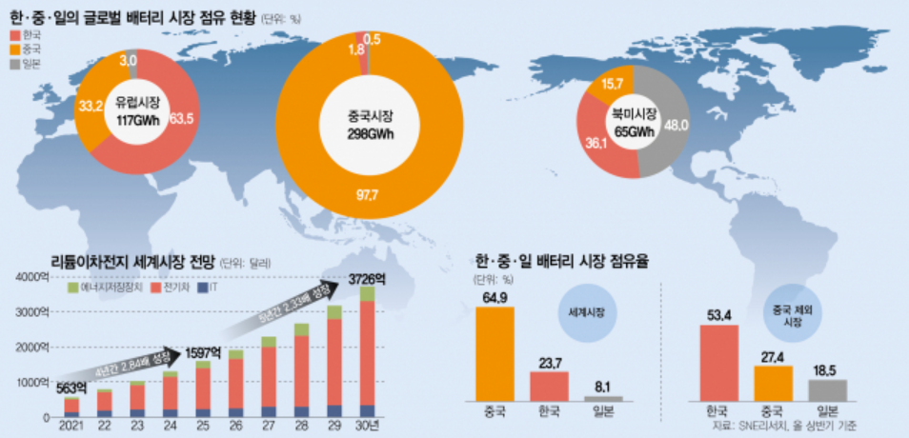
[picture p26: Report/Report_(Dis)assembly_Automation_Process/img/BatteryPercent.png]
Battery market share
|  |
| :-----------------------------------------------: |
|        **Figure 1.** Battery Market Share         |
This project aims to address these challenges by developing an **automated battery cell winding process using industrial robots integrated with machine vision and artificial intelligence technologies**. By combining robotic manipulation, sensor-based detection nodes, state diagram–based control logic, and camera-based recognition of battery cells and winding components, the project seeks to transform a labor-intensive process into a high-speed, high-precision automated system. Through this approach, the feasibility of improving productivity, reliability, and safety in battery manufacturing and recycling processes is investigated.

## II. Problem Statement
---
### 1. Problems
1. Minor process deviations create potential defects, leading to battery failures and safety hazards.
    
2. In mass production, significant process variation creates challenges in ensuring uniformity.
    
3. Conventional defect inspection methods are slow and only detect surface defects.

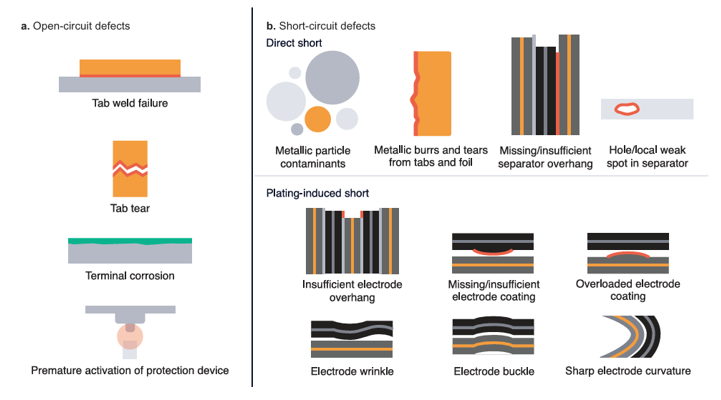
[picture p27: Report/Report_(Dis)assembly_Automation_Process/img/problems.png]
Cell Problem Types
|  |
| :---------------------------------------: |
|     **Figure 2.** Cell Problem Types      |

### 2. Project Objectives

The main objectives of this project are as follows:

1. **Implementation of Automated Assembly and Disassembly of Battery Cell Winding Processes**
    To automate the assembly and disassembly of battery cells and winding components using industrial robots, thereby minimizing human error and improving repeatability.
2. **Development of a Machine Vision–Based Recognition System**
    To detect battery cell positions, orientations, and conditions (normal or defective) using camera-based vision systems and AI models, and to integrate the recognition results into the robot control system.
3. **Design of Robot Control Logic and State Diagrams**
    To design structured state diagrams that manage process flow and ensure stable coordination between sensor detection nodes and robotic actions.
4. **Verification of Process Reliability and Performance**
    To experimentally evaluate the success rate, accuracy, and operational stability of the automated system and assess its applicability to real industrial environments.

### 3. Expected Outcomes

The expected outcomes of this project are as follows:

1. **Improved Productivity and Operational Efficiency**
    By replacing manual labor with robotic automation, continuous operation beyond traditional working hours becomes possible, significantly increasing overall productivity.
2. **Enhanced Accuracy and Quality Consistency**
    The automated system is expected to achieve a high success rate in assembly and disassembly tasks, while the machine vision system enables reliable identification of normal and abnormal battery cells, excluding specific inclusion cases.
3. **Reduced Labor Dependency and Improved Workplace Safety**
    Automating repetitive and potentially hazardous battery handling processes reduces worker exposure to risk and lowers dependence on skilled manual labor.
4. **Scalability for Battery Recycling and Future Smart Factory Applications**
    The proposed system can be extended to battery disassembly and recycling processes, providing a technological foundation for advanced smart factory and sustainable battery production systems.

### 4. Evaluation Index

| Process | Target |
| :---: | :---: |
|  **UR5 Robot Operation** | - Bracket detection success rate ≥ 98% <br />- Cell box detection success rate = 100% <br />- Pick and Place success rate ≥ 95% <br />- Stopper linkage success rate = 100% <br />- Assembly/Disassembly process completion time ≤ 1 minute |
| **Indy10 Robot Operation** | - Cell orientation detection success rate = 100% <br />- Foreign object detection success rate ≥ 95% <br />- Defective cell detection success rate ≥ 95% <br />- Stopper linkage success rate = 100% <br />- Winding assembly/disassembly process completion time ≤ 1 minute |
| **Defect Detection** | - Defect detection success rate (cylindrical surface) ≥ 95% <br />- Defect detection success rate (flat surface) ≥ 80% |

## III. Requirements
---
### 1. Hardware List

- UR5e
	- 2-finger gripper
- Cell & Wind

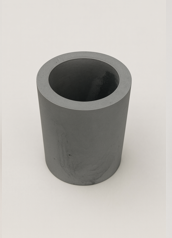
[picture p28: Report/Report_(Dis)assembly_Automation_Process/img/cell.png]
Cell
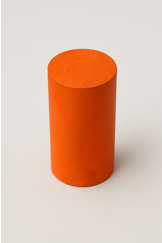
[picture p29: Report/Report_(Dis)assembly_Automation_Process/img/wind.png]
Wind
|  |  |
| :---: | :---: |
| **Figure 3A.** Cell | **Figure 3B.** Wind |
- Bracket

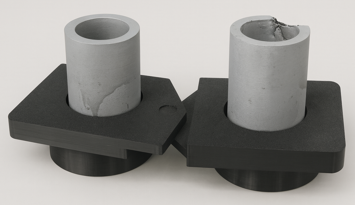
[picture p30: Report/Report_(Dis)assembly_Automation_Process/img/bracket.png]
Bracket
|  |
| :---------------------------: |
|     **Figure 4.** Bracket     |
- Cell Box
- Slide Rail
- Stepper Moters & Stopper
- Ultrasonic Sensor

### 2. Software List

- OS: Linux Ubuntu 20.04
- ROS: ROS Noetic
- Additional Packages Required
	- OpenCV
	- numpy
- Additional Ubuntu Utility Programs
	- Python 3.10.8
	- terminator
To build overall software setting, follow the [link](https://github.com/ykkimhgu/HGU_IAIA/tree/main/Tutorial/TU_ROS_v2) for extra guideline.
## IV. Procedure
---
This report covers the camera-based cell and winding **disassembly and assembly automation process (UR robot)**.
- [disassembly and assembly automation](https://github.com/Joungbin-C/IAIA_Robot_Automation_25-2/tree/main/Report/Report_(Dis)assembly_Automation_Process/Report_(Dis)Assembly_Automation.md)

Process recognition-based **pick and place automation (Indy10)** and deep learning-based **cell defect detection** are covered in the following links.

- [pick and place automation](https://github.com/Joungbin-C/IAIA_Robot_Automation_25-2/blob/main/Report/Report_(De)Compose_process/Report_(De)Compose_process.md)
- [cell defect detection](https://github.com/Joungbin-C/IAIA_Robot_Automation_25-2/blob/main/Report/Report_MachinVision.pdf)

### 1. Overview

This system's process involves recognizing objects using image processing techniques, then using relative coordinate-based robot control to precisely grasp and place them in designated locations. Process stability is ensured through a step-by-step structure of detection, correction, movement, and gripping. Furthermore, the robot detects whether cells are present in a cell box and determines the appropriate assembly and disassembly processes accordingly.

### 2. Logic Design

Based on the tasks listed above, the system's flowchart is drawn as below:

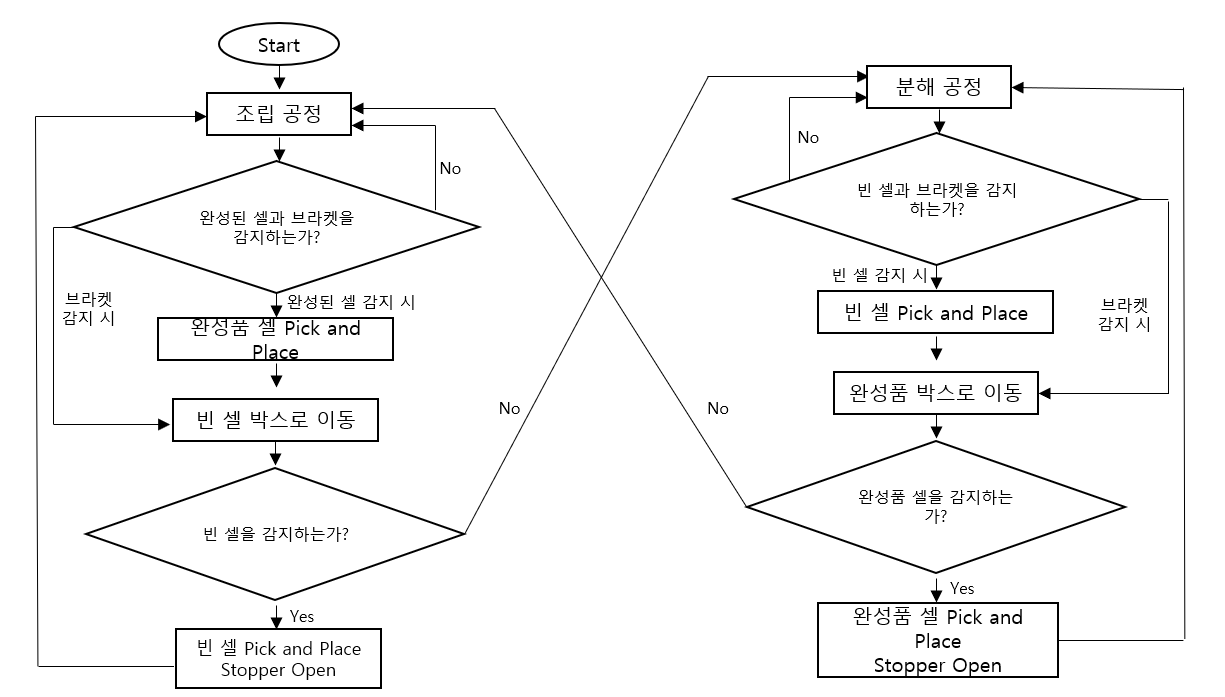
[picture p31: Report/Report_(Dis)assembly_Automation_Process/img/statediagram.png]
State Diagram
|  |
| :--------------------------------------: |
|       **Figure 5.** State Diagram        |

### 3. Assembly Process

- **State 1**: First Bracket Detection (State 2 if Composite is detected, State 5 if Bracket is detected)
- **State 2**: Place Composite in Cell Box, then State 3
- **State 3**: Second Bracket Detection (State 4 if Composite is detected, State 6 if Bracket is detected)
- **State 4**: Place Composite in Cell Box, then State 5
- **State 5**: Pick a cell from the cell box, place it on the bracket, then State 6 (if no cell is in the cell box, then State 101 (Disassembly Process))
- **State 6**: Pick a cell from the cell box, place it on the bracket, then reset to State 1 (if no cell is in the cell box, then State 201 (Disassembly Preparation Process))

### 4. Disassembly Process

- **State 101**: First Bracket Recognition (State 102 for cell detection, State 105 for bracket detection)
- **State 102**: Place the cell in the cell box, then State 103
- **State 103**: Second bracket recognition (State 4 for cell detection, State 106 for bracket detection)
- **State 104**: Place the cell in the cell box, then State 5
- **State 105**: Pick the composite from the cell box, then place it on the bracket, then State 106 (if there is no composite in the cell box, then State 1 (assembly process))
- **State 106**: Pick the composite from the cell box, then place it on the bracket, then reset to State 101 (if there is no composite in the cell box, then State 301 (assembly preparation process))

### 5. Disassembly Preparation Process

- **State 201**: First bracket recognition (if there is a composite, place it in the cell box, then State 101 (disassembly process) and State 202 for bracket detection)
- **State 202**: Detect a composite in the second bracket, place it in the cell box, and switch to State 101 (disassembly process).

### 6. Assembly Preparation Process

- **State 301**: First bracket recognition (if a cell is detected, place it in the cell box, then switch to State 1 (assembly process). If a bracket is detected, switch to State 302.)

- **State 302**: Detect a cell in the second bracket, place it in the cell box, and switch to State 1 (assembly process).

### 7. Image Processing

The following image processing was used to identify the battery cell and assembly/disassembly process status.

**1. yellow_bracket_detection_node.py**
- This sensor node detects the bracket holes in the yellow bracket.
	**Bracket (yellow circle) detection**
```python
mask = cv2.inRange(hsv, [20,120,120], [32,255,255])
circles = cv2.HoughCircles(mask, cv2.HOUGH_GRADIENT,
                           dp=1.2, minDist=190,
                           minRadius=210, maxRadius=430)
x, y, r = max(circles, key=lambda c: c[2])

```

- HSV-based yellow segmentation followed by Hough Circle circular bracket detection.
- Since the brackets are of constant size, false detections can be eliminated within the radius range.

	**EMA Filter**
```python
x = (1-α)*x_prev + α*x
y = (1-α)*y_prev + α*y
```

- Removing frame-to-frame positional blur with EMA filters

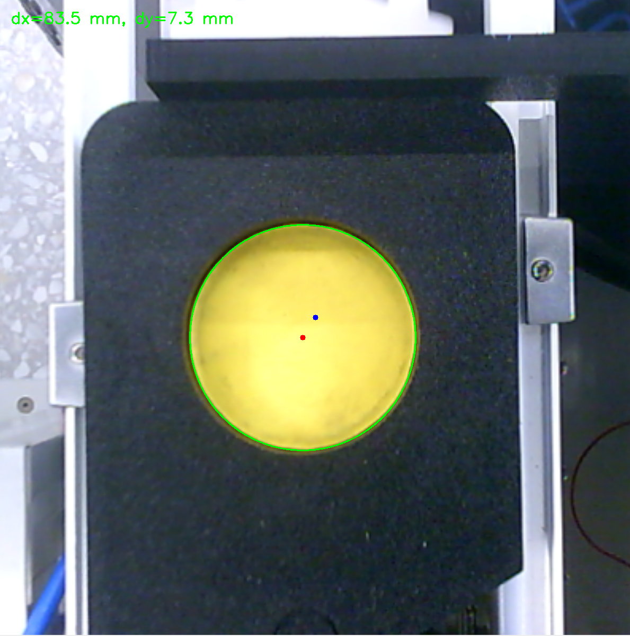
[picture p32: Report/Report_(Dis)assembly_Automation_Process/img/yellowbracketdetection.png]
Yellow Bracket Detection
|  |
| :-----------------------------------------------------------: |
|                **Figure 6.** Bracket Detection                |

**2. filled_cellbox_detection_node.py**
- This detection node detects cells in an empty cell box.
	**Cell box brightness detection technique (classical image processing)**
```python
bright_mask = np.all(cell_roi >= 215, axis=2)
ratio = np.sum(bright_mask) / cell_area
```
- This detection technique is a classical computer vision method that uses RGB color space-based threshold brightness detection.
- Pixels within each cell region whose R, G, and B channel values all exceed a threshold are defined as bright pixels. If the area ratio of these pixels exceeds a threshold, the cell is determined to be detected.

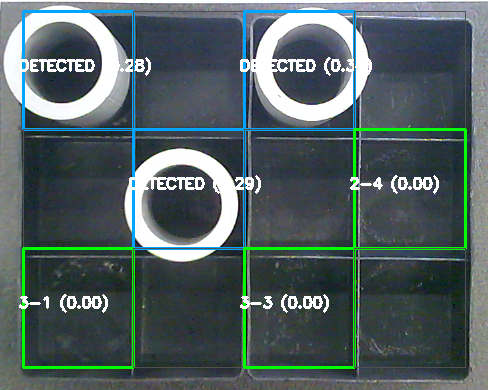
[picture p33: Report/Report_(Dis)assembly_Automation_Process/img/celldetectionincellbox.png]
Cell Detection in Cellbox
|  |
| :------------------------------------------------------------: |
|            **Figure 7.** Cell Detection in Cellbox             |

**3. empty_composite_cellbox_detection_node.py**
- This detection node detects empty boxes in the composite cell boxes.
	**Cell detection technique (classical image processing)**
```python
mean_intensity = np.mean(cell_region)
if mean_intensity < 90:
    detected = True
```
- This technique is a classical computer vision method that uses grayscale average intensity-based threshold detection.
- If the mean intensity of each grid cell area falls below a threshold, the cell is considered dark and is then detected as a location for a composite cell.

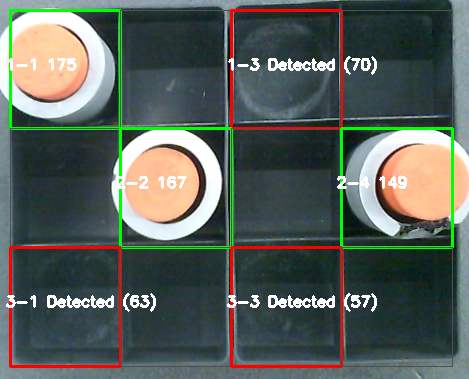
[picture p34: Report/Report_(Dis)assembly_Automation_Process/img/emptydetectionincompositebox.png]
Empty Composite Detection in Cellbox
|  |
| :-----------------------------------------------------------------------------: |
|                  **Figure 8.** Empty Composite Cell in Cellbox                  |

**4. filled_composite_cellbox_detection_node.py**
- This detection node detects composite cells in the finished cell box.
	**Composite cell detection core logic**
```python
orange_mask = cv2.inRange(cell_roi,
                          (65,110,220), (185,220,255))
ratio = np.sum(orange_mask > 0) / cell_area
```
- This node is a classical computer vision technique that uses threshold color detection based on the RGB (BGR) color space.
- If the percentage of pixels within each cell that fall within the orange range exceeds a certain threshold (≥5%), then the cell is considered detected.

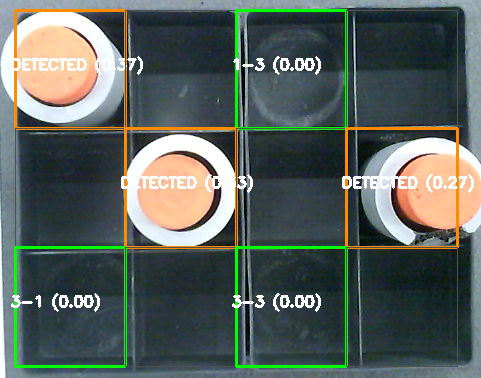
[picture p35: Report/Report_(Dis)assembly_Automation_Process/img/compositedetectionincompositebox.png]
Filled Composite Detection in Cellbox
|  |
| :----------------------------------------------------------------------------------: |
|                    **Figure 9.** Filled Composite Cell in Cellbox                    |

**5. empty_cell_cellbox_detection_node.py
- This detection node detects empty spaces in empty cell boxes.
	**Empty space detection core logic**
```python
black_mask = cv2.inRange(hsv_roi, lower_black, upper_black)
```
- It is a threshold-based classical image processing technique that determines the presence of a black object based on the ratio of pixels with low brightness (V) in the HSV color space.

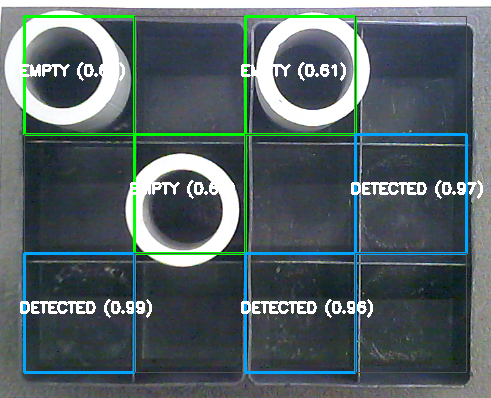
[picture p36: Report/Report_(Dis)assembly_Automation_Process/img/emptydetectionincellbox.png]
Empty Composite Detection in Cellbox
|  |
| :------------------------------------------------------------------------: |
|                    **Figure 10.** Empty Cell in Cellbox                    |

**6. winding_decect_node.py**
- This sensor node detects the wind.
	**Wind detection core logic**
```python
circles = cv2.HoughCircles(gray_blurred, cv2.HOUGH_GRADIENT, ...)
orange_ratio = orange_pixels_inside_circle / circle_area
```
- It is a classical image processing technique that detects circular objects using grayscale-based Hough Circle Transform and determines them as valid objects only when the proportion of orange pixels inside the detected circle exceeds a threshold.

**7. composite_detection.py**
- This detection node detects the composite cell.
	**Composite cell detection core logic**
```python
circles = cv2.HoughCircles(gray_blurred, cv2.HOUGH_GRADIENT, ...)
```
- It is a classical image processing technique that detects circular objects by applying Hough Circle Transform to a grayscale threshold image within the central ROI, and determines them as valid locations only when the center distance condition is satisfied.

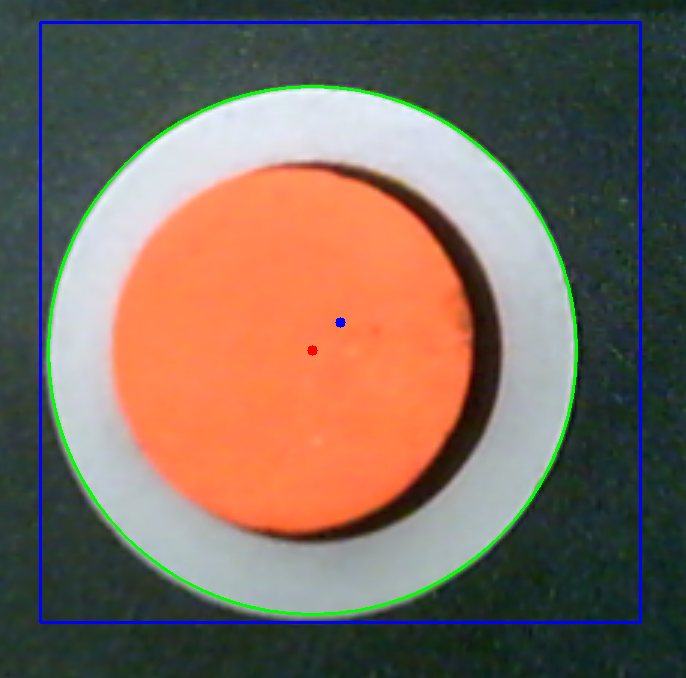
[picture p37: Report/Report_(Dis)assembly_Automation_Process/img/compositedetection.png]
Composite Detection
|  |
| :--------------------------------------------------: |
|          **Figure 11.** Composite Detection          |

**8. cell_detection.py
- This detection node detects empty cells.
	**Empty cell detection core logic**
```python
circles = cv2.HoughCircles(gray_blurred, cv2.HOUGH_GRADIENT, ...)
```
- It is a rule-based classical image processing technique that detects circular objects by applying Hough Circle Transform to grayscale threshold images, and judges them as pure gray objects only when the orange/yellow ratio inside the circle is below the threshold.

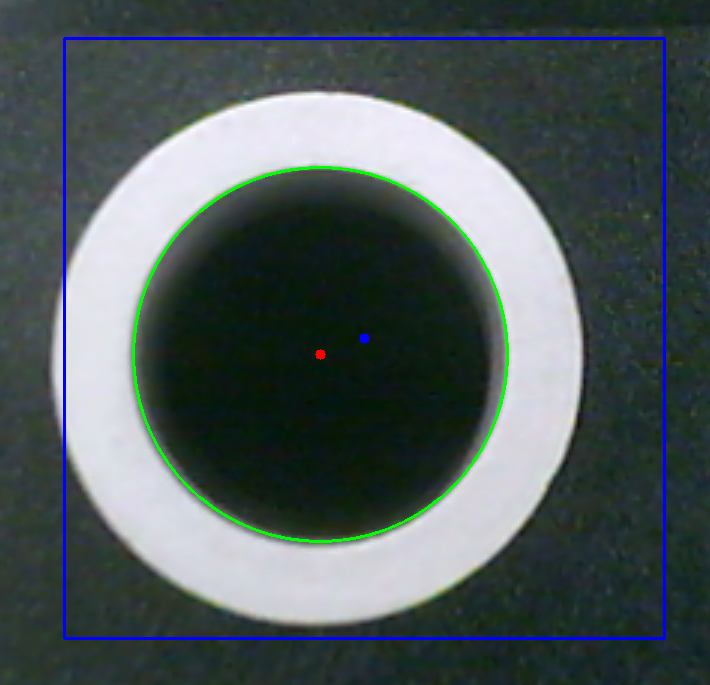
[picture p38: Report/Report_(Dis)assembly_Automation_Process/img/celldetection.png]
Cell Detection
|  |
| :----------------------------------------: |
|       **Figure 12.** Cell Detection        |

### 8. Pick and Place Algorithm(Manipulation)

**1. Joint-based locomotion (MoveJ)**
```python
def goJ(self, arr_deg, label=""):
    ok = self.ur5e.go_to_joint_abs(self.jdeg(arr_deg))
    rospy.sleep(1.5)
    return ok
```
- Meaning: Move the UR5e relative to absolute joint coordinates using a predefined array of joint angles.
- Usage: Stable pose transitions, such as observation poses, grid access, and return poses.

**2. Cartesian movement based on relative coordinates (XY/Z separation)**
```python
self.ur5e.go_to_pose_rel([dx, dy, 0.0], [0, 0, 0])
self.ur5e.go_to_pose_rel([0.0, 0.0, -0.07], [0, 0, 0])
```
- Meaning: Relative movement relative to the current TCP
- Features: After moving in the XY plane, only the Z axis is lowered/raised → Minimizes collisions
- Usage: Vision-based fine-position correction pick-and-place

**3. Pick Basic Sequence**
```python
# XY 이동
self.ur5e.go_to_pose_rel([dx, dy, 0.0], [0,0,0])
# Z 하강
self.ur5e.go_to_pose_rel([0.0, 0.0, -0.07], [0,0,0])
# 그립 ON
self.grip_on_6s()
# Z 상승
self.ur5e.go_to_pose_rel([0.0, 0.0, 0.115], [0,0,0])
```
- Meaning: Typical industrial robot pick sequence
- Feature: Reuse of the same structure for all pick operations

**4. Grid-based Pick Cycle (Reusable Blocks)**
```python
def pick_cycle(self, pose_dict, cell_key, grip_mode="off"):
    self.goJ(p["start"])
    self.goJ(p["pick"])
    if grip_mode == "on": self.grip_on_6s()
    else: self.grip_off_6s()
    self.goJ(p["start"])
```
- Meaning: Cell name (e.g., "2-3") → Automatically execute the corresponding joint pose.
- Usage:
	- Move to the grid containing the cell. 
	- Later, calculate the relative coordinates and execute Pick or Place.

**5. State-based robot motion transition (FSM)**
```python
if self.state == 1: self.state_1()
elif self.state == 5: self.state_5()
elif self.state == 101: self.state_101()
```
- Meaning: Manage robot motion scenarios as states based on detection results.
- Features:
	- Assembly Process
	- Disassembly Process

This system consists of an industrial robot control logic that combines joint-based movement and Cartesian relative movement and performs pick-and-place operations through an FSM structure.

## V. Results
---
### 1. Results

The test was performed a total of 100 times, and the process time was measured from the moment the stopper contacted the bracket until the stopper opened after the process was completed. The results are as follows.

| Process | Goal | Result |
| --- | :---: | :---: |
| Detection | - Bracket detection success rate ≥98%<br>- Cell box detection success rate =100% | - Bracket Detection Success Rate = 100%<br>- Cell Box Detection Success Rate = 100% |
| Pick and Place | - Pick and Place Success Rate ≥95% | - Pick and Place Success Rate = 97% |
| Stopper linkage and process completion time | - Stopper Interlock Success Rate = 100%<br>- Assembly/Disassembly Process Completion Time: Within 1 Minute | - Stopper Interlock Success Rate = 100%<br>- Assembly/Disassembly Process Completion Time: 1 minute 35 seconds |

### 2. Discussion

1. While the pick-and-place operation met the target performance indicator of a success rate of over 95%, the battery cell assembly and disassembly process requires precise analysis, as even a single failure can impact the overall process quality. The reason is that the `go_to_joint_rel()` function used in relative coordinate-based control sets the positioning error tolerance to 0.003, allowing for a maximum error of approximately 3 mm. However, indiscriminately reducing this tolerance value improves positioning accuracy, but there is a trade-off: increased path calculation time and overall process delays. Therefore, more detailed adjustments to the tolerance value are necessary to simultaneously satisfy the required process accuracy and computational efficiency.
2. The target process time of less than one minute was not met, requiring further analysis in this area. The Cartesian technique, which directly specifies the spatial coordinates (X, Y, Z) of the robot and moves it, has no risk of sign inversion of the posture (yaw, pitch, roll) and can secure high precision because the path is calculated by dividing it into intervals of about 2 mm. However, it has the limitation of relatively slow process speed. On the other hand, the Euler technique, which directly controls the posture (yaw, pitch, roll) of the end-effector, has fast movement speed, but a serious problem has been observed in which the sign inversion of the posture occurs in certain situations and the robot posture suddenly becomes distorted, which acts as a clear trade-off. In addition, a delay of about 1.5 seconds occurred in the process of calling the detection node in a callback manner, which is believed to be caused by the ROS communication structure itself rather than the delay caused by `rospy.sleep()`.
3. Since the image processing was performed based on the lighting standard of NTH 115, detection and pick and place may become more inaccurate when exposed to other lighting environments.
4. If neither the Cell nor the Composite box contains a single cell, the ur5e robot will continue to switch between process states. Therefore, at least one cell must be present in each box.
5. The Cell box must have a Cell in its proper location, and the Composite box must have a Composite Cell in its proper location. Otherwise, the cell will not be recognized.

## VI. Conclusion
---
By introducing a process-aware pick and place automation system, operating hours can be significantly extended compared to existing human-driven processes, enabling continuous 24-hour operation. While the cycle time was somewhat long at 1 minute and 35 seconds, and only two cells were picked and placed per cycle, this project demonstrated the feasibility of fully unmanned pick and place, suggesting potential savings in labor and operating costs.
Future research will focus on shortening the overall process execution time and enhancing the precision of image processing detection to ensure a near-zero pick and place failure rate.

## VII. Reference

1. 박예나. (2024년 11월 17일). “배터리 삼국지”… 中 질주 속 K배터리의 난제는. 서울경제. [https://www.sedaily.com/NewsView/29X4QWC74S](https://www.sedaily.com/NewsView/29X4QWC74S)

2. Attia, P. M., Moch, E., & Herring, P. K. (2025). Challenges and opportunities for high-quality battery production at scale. Nature Communications, 16, 611. [https://doi.org/10.1038/s41467-025-55861-7](https://doi.org/10.1038/s41467-025-55861-7)

3. Jiang, X., Gramopadhye, A.K., Melloy, B.J. and Grimes, L.W. (2003), Evaluation of best system performance: Human, automated, and hybrid inspection systems. Hum. Factors Man., 13: 137-152. https://doi.org/10.1002/hfm.10031

4. Jo, H., Park, H., Baek, S., & Kang, E. K. (2017). Low back pain in farmers: The association with agricultural work management, disability, and quality of life in Korean farmers. Human Factors and Ergonomics in Manufacturing & Service Industries, 27(3), 156–165. https://doi.org/10.1002/hfm.20699

## VIII. Command execution order

### 1. Structure

```
catkin_ws
	|- build
	|- devel
	|- packages_from_git
	|- src
	|----|- CMakeLists.txt
	|----|- 22000167_Kiminyeop_ur_python
	|----|----|- msg
	|----|----|----| grip_command.msg
	|----|----|----| grip_state.msg
	|----|----|----| object_info.msg
	|----|----|----| pet_info.msg
	|----|----|----| robot_state.msg
	|----|----|- src
	|----|----|----| camera.py
	|----|----|----| cell_detection.py
	|----|----|----| composite_detection.py
	|----|----|----| empty_cell_box_detection_node.py
	|----|----|----| empty_composite_cellbox_detection_node.py
	|----|----|----| filled_cellbox_detection_node.py
	|----|----|----| filled_composite_cellbox_detection_node.py
	|----|----|----| main.py
	|----|----|----| move_group_python_interface.py
	|----|----|----| winding_detect_node.py
	|----|----|----| yellow_bracket_detection_node.py
```
`my_robot_calibration.yaml` will add to the home

### 2. Command

1. If you saved my_robot_calibration.yaml to your home directory, run the following. If the path doesn't exist, you'll need to reset it to match your computer's path.
```
chmod+x/~my_robot_calibration.yaml
```

2. Since the project is based on ROS environment, every command line is done under catkin workspace directory.
```
cd~/catkin_ws
catkin_make
roscore
```

3. To activate the system, the robot should be connected to a computer. Communication protocol is TCP/IP based therefore, IP should be set in proper manner
```
roslaunch ur_robot_driver ur5e_bringup.launch robot_ip:=192.168.0.2
roslaunch ur5e_rg2_moveit_config move_group.launch
```

4. Connect camara in UR5e
```
chmod +x ~/catkin_ws/src/ur_python/src/camera.py
rosrun 22000167_Kiminyeop_ur_python camera.py
```

5. Follow the steps below

- Empty Bracket Detection: This detection node detects yellow bracket holes.
```
chmod +x ~/catkin_ws/src/ur_python/src/yellow_bracket_detection_node.py
rosrun 22000167_Kiminyeop_ur_python yellow_bracket_detection_node.py
```

- Cell Box Cell Detection: This detection node detects cells in empty cell boxes.
```
chmod +x ~/catkin_ws/src/ur_python/src/filled_cellbox_detection_node.py
rosrun 22000167_Kiminyeop_ur_python filled_cellbox_detection_node.py
```

- Empty Completed Box Detection: This detection node detects empty boxes in completed cell boxes. 
```
chmod +x ~/catkin_ws/src/ur_python/src/empty_composite_cellbox_detection_node.py
rosrun 22000167_Kiminyeop_ur_python empty_composite_cellbox_detection_node.py
```

- Completed Cell Box Detection: This detection node detects cells in a completed cell box.
```
chmod +x ~/catkin_ws/src/ur_python/src/filled_composite_cellbox_detection_node.py
rosrun 22000167_Kiminyeop_ur_python filled_composite_cellbox_detection_node.py
```

- Empty Cell Box Detection: This detection node detects empty boxes in an empty cell box. 
```
chmod +x ~/catkin_ws/src/ur_python/src/empty_cell_cellbox_detection_node.py
rosrun 22000167_Kiminyeop_ur_python empty_cell_cellbox_detection_node.py
```

- Orange Winding Detection: This detection node detects orange windings.
```
chmod +x ~/catkin_ws/src/ur_python/src/winding_detect_node.py
rosrun 22000167_Kiminyeop_ur_python winding_detect_node.py
```

- Completed Cell Detection: This detection node detects completed cells. 
```
chmod +x ~/catkin_ws/src/ur_python/src/composite_detection.py
rosrun 22000167_Kiminyeop_ur_python composite_detection.py
```

8. Cell Detection: This detection node detects empty cells.
```
chmod +x ~/catkin_ws/src/ur_python/src/cell_detection.py
rosrun 22000167_Kiminyeop_ur_python cell_detection.py
```

- Run Arduino Stopper
	After installing Arduino 1.8.19, confirm that the board is Arduino Uno in the tool bar and that the port is dev/tty/ACM0. Confirm and upload, then close the Arduino window.

10. Enter VScode and run main.py.

### 3. Troubleshooting

1. If the robot movement doesn't work, it's almost always due to a problem with 
```
roslaunch ur_robot_driver ur5e_bringup.launch robot_ip:=192.168.0.2
``` 
Therefore, undoing and re-running this terminal should resolve the issue.

2. If you run the code 
```
chmod +x ~/catkin_ws/src/ur_python/src/camera.py
rosrun 22000167_Kiminyeop_ur_python camera.py
```
the camera may not be connected to the ur5e robot but to the laptop. In this case, adjust the numeric value of `self.cap = cv2.VideoCapture(2)`
from 0 to 5 and then run the program.

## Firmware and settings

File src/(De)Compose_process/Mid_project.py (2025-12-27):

#!/usr/bin/env python3
# -*- coding:utf-8 -*-

import rospy, time
from math import radians, tau
from indy_driver.msg import comp_wind_info, decomp_wind_info, bracket_info, comp_pose_info, cell_state_info, process_info, comp_pose_info, decomp_pose_info
from move_group_python_interface import MoveGroupPythonInterface
import serial
import math  

CELL_JOINTS_ABS = {
    1: [radians(x) for x in [17.07, 30.93, 16.57, -0.03, 131.63, 17.10]],
    2: [radians(x) for x in [11.63, 26.03, 26.64, -0.04, 127.02, 11.78]],   
    3: [radians(x) for x in [ 5.37, 25.02, 26.48, -0.00, 128.23,  5.71]],
    4: [radians(x) for x in [19.07, 20.99, 30.35, -0.09, 127.19, 19.25]],
    5: [radians(x) for x in [13.29, 19.97, 31.78,  0.00, 128.77, 13.87]],
    6: [radians(x) for x in [ 6.08, 16.91, 35.98, -0.00, 127.54,  6.10]],
}

CELL_JOINTS_ABS2 = {
    1: [radians(x) for x in [16.72, 21.16, 43.88,  0.39, 114.90, 17.07]],
    2: [radians(x) for x in [11.30, 19.38, 46.29,  0.39, 115.25, 11.73]],   
    3: [radians(x) for x in [ 5.37, 16.04, 50.65, -0.00, 113.16,  5.71]],
    4: [radians(x) for x in [19.08, 11.63, 56.12, -0.09, 110.74, 19.27]],
    5: [radians(x) for x in [13.29, 10.88, 57.02,  0.00, 112.63, 13.87]],
    6: [radians(x) for x in [ 6.08,  8.52, 59.77, -0.00, 112.12,  6.20]],
}

CELL_JOINTS_ABS3 = {
    1: [radians(x) for x in [19.67,  9.80, 53.00, -0.00, 117.16, 19.80]],
    2: [radians(x) for x in [13.43,  7.42, 55.75,  0.00, 116.82, 13.46]],
    3: [radians(x) for x in [ 6.47,  4.28, 59.21,  0.05, 116.49,  6.57]],
    4: [radians(x) for x in [22.67,  2.03, 61.60, -0.01, 116.34, 22.75]],
    5: [radians(x) for x in [15.69, -0.06, 63.89, -0.21, 116.23, 15.54]],
    6: [radians(x) for x in [ 7.65, -2.15, 65.78, -0.24, 116.40,  7.53]],
}

check_pose          = [radians(x) for x in [ 13.65,  16.27 , 34.63,  0.00, 129.09, 13.64]]               # checking windings
comp_pose           = [radians(x) for x in [ 56.29,  -7.47 , 61.91,  0.00, 125.55, 56.31]]               # checking braket is arriver
comp_pose_place1    = [radians(x) for x in [ 46.36,  -3.20 , 62.98,  0.00, 120.70, 46.04]]               # bracket num 1
comp_pose_place2    = [radians(x) for x in [ 27.50, -13.75 , 71.86,  0.13, 122.30, 27.02]]               # bracket num 2
decomp_pose_place1  = [radians(x) for x in [ 58.23, -11.81 , 73.84, -0.00, 118.35, 57.75]]               # checking braket num 1 in decomp mode
decomp_pose_place2  = [radians(x) for x in [ 39.24, -25.30 , 82.55, -0.13, 122.75, 38.73]]               # checking braket num 2 in decomp mode
trash_pose          = [radians(x) for x in [100.02,  39.10 , 20.85,  0.01, 118.76, 46.65]]               # trash position
b_arrive_check_pose = [radians(x) for x in [ 58.66,  -6.64 , 60.56,  0.32, 127.38, 59.84]]               # checking braket is arrive


class IndyPickPlaceNode:
    def __init__(self):
        self.robot = MoveGroupPythonInterface(real=True, gripper="Gripper")
        self.latest_comp_wind   = None                                          
        self.latest_decomp_wind = None
        self.latest_bracket     = None
        self.latest_flag        = None  # 1~4
        self.latest_decomp_pose = None
        self.latest_comp_pose   = None
        self.process_flag       = None  # compose or decompose
        self.iteration_count    = 0
        self.MAX_ITER           = 6  
        self.first              = None
        self.second             = None

        # --- Subscribers --- #
        rospy.Subscriber("comp_wind_info"  , comp_wind_info  , self.comp_wind_callback  )             # image_Display1
        rospy.Subscriber("decomp_wind_info", decomp_wind_info, self.decomp_wind_callback)             # image_Display6
        rospy.Subscriber("bracket_info"    , bracket_info    , self.bracket_callback    )             # image_Display2    = Bracket 도착여부
        rospy.Subscriber("comp_pose_info"  , comp_pose_info  , self.comp_pose_callback  )             # image_Display3
        rospy.Subscriber("cell_state_info" , cell_state_info , self.cell_state_callback )             # Mid_communication
        rospy.Subscriber("process_info"    , process_info    , self.process_callback    )             # image_Display4    = Process 결정여부
        rospy.Subscriber("decomp_pose_info", decomp_pose_info, self.decomp_pose_callback)             # image_Display5


        # --- Arduino Serial (모터 제어) --- #
        try:
            self.ser = serial.Serial('/dev/ttyACM0', 115200, timeout=1)  # 포트는 환경에 맞게 변경
            rospy.sleep(2.0)  # 아두이노 자동 리셋 대기
            rospy.loginfo("🔌 Arduino serial connected.")
        except Exception as e:
            self.ser = None
            rospy.logwarn(f"⚠️ Arduino serial open failed: {e}")

        rospy.loginfo("🤖 [indy_pick_place] Initialized and waiting for cell/place info...")

    # ========================================================================= #  
    # =========================== Callback Function =========================== #
    def comp_wind_callback(self, msg):                                                       
        self.latest_comp_wind = int(msg.cell_num)

    def decomp_wind_callback(self, msg):
        self.latest_decomp_wind = int(msg.cell_num)

    def bracket_callback(self, msg):
        self.latest_bracket = (msg.center_x, msg.center_y)

    def cell_state_callback(self, msg: cell_state_info):
        self.latest_flag = int(msg.flag)  
        rospy.loginfo(f"[cell_state] Updated flag={self.latest_flag}")


    def process_callback(self, msg):
        self.process_flag = int(msg.flag) 

    def comp_pose_callback(self, msg):
        self.latest_comp_pose = (msg.center_x, msg.center_y)

    def decomp_pose_callback(self, msg):
        self.latest_decomp_pose = (msg.center_x, msg.center_y)

    # ========================================================================= #  
    # ============================= Wait Function ============================= #
    def wait_until_wind_ready(self):
        rate = rospy.Rate(50)  # 50Hz
        while not rospy.is_shutdown():
            c = self.latest_comp_wind
            if c is not None :  
                return c
            rospy.loginfo_throttle(1.0, "🕓 Waiting for valid cell ...")
            rate.sleep()


    def wait_until_bracket_ready(self):
        rate = rospy.Rate(50)  # 50 Hz
        while not rospy.is_shutdown():
            p = self.latest_bracket
            if p is not None:
                x, y = p
                if math.isfinite(x) and math.isfinite(y):
                    return (x, y)
            rospy.loginfo_throttle(1.0, "🕓 Waiting for valid bracket (not NaN)...")

    def wait_until_process_ready(self):
        rate = rospy.Rate(50)  # 50 Hz polling
        while not rospy.is_shutdown():
            f = getattr(self, "process_flag", None)  # 혹시 변수 미정의 상태 대비
            if f in (0, 1):  
                rospy.loginfo(f"✅ process_flag received: {f} ({'compine' if f == 1 else 'decompose'})")
                return f
            rospy.loginfo_throttle(1.0, "🕓 Waiting for process_flag (0=decompose, 1=compine)...")
            rate.sleep()

    def wait_until_decomp_pose_ready(self):
        rate = rospy.Rate(50)  # 50Hz
        while not rospy.is_shutdown():
            p = self.latest_decomp_pose
            if p is not None:
                cx, cy = p
                if math.isfinite(cx) and math.isfinite(cy):
                    rospy.loginfo(f"✅ decompose pose ready: ({cx:.4f}, {cy:.4f})")
                    return (cx, cy)
            rospy.loginfo_throttle(1.0, "🕓 Waiting for valid decompose pose (not None/NaN)...")


    # ============================ Arduino Function =========================== #
    # ========================================================================= #  

    def open_stopper(self):
        """아두이노에 'o' 문자 전송 → 모터 오픈"""
        if not hasattr(self, 'ser') or self.ser is None:
            rospy.logwarn("⚠️ Arduino serial not available.")
            return
        try:
            self.ser.write(b'o')
            self.ser.flush()
            rospy.loginfo("📨 Sent 'o' to Arduino (open stopper).")
        except Exception as e:
            rospy.logwarn(f"⚠️ Failed to send 'o' to Arduino: {e}")



    def compose_process(self, cell):
        rospy.loginfo(f"🚀 Starting iteration {self.iteration_count+1}/{self.MAX_ITER} )")
        start = time.time()

        flag  = self.latest_flag
        rospy.loginfo(f"{flag}")
        if flag is None :
            flag = 1

        if flag == 1:
            self.first  = 1
            self.second = 1
        elif flag == 2:
            self.first  = 3
            self.second = 1
        elif flag == 3:
            self.first  = 1
            self.second = 3
        elif flag == 4:
            self.first  = 3
            self.second = 3
        elif flag == 5:
            self.first  = 1
            self.second = 2
        elif flag == 6:
            self.first  = 3
            self.second = 2
        else :
            self.first  = 1
            self.second = 1

        

        try:
            if self.first == 1 :
                #====================================================== PICK ======================================================================#
                self.robot.go_to_joint_abs(check_pose)
                rospy.sleep(0.5)

                if self.latest_comp_wind is None:
                    self.wait_until_wind_ready()
                
                if self.latest_comp_wind in (0,6):
                    rospy.loginfo (("⚠️ End compose process"))
                    return
                    
                wind = self.latest_comp_wind
                rospy.loginfo(f"📦 Updated cell from callback: {wind}")

                target_joints = CELL_JOINTS_ABS3.get(wind)
                self.robot.go_to_joint_abs(target_joints)
                rospy.sleep(0.5)

                cx, cy = self.latest_comp_pose
            
                self.robot.go_to_pose_rel([-cy, cx, 0.0],[0,0,0])
                rospy.sleep(0.5)

                self.robot.go_to_pose_rel([0.0,0.0, -0.04],[0,0,0])
                rospy.sleep(0.5)

                self.robot.grip_on()
                rospy.sleep(1)

                self.robot.go_to_joint_rel([0, radians(-8.0), 0, 0, radians(-5.0), 0])
                rospy.sleep(0.5)
            
                #====================================================== PLACE =====================================================================#
                self.robot.go_to_joint_abs(comp_pose_place1)
                rospy.sleep(0.5)

                self.robot.grip_off()
                rospy.sleep(1)

            if self.second == 1:
                #=================================================================================================================================#
                #====================================================== PICK ======================================================================#
                self.robot.go_to_joint_abs(check_pose)
                rospy.sleep(0.5)

                if self.latest_comp_wind is None:
                    self.wait_until_wind_ready()
                
                # if self.latest_comp_wind == 6:
                #     rospy.loginfo (("⚠️ There is no cell: End compose process"))
                #     return
                wind = self.latest_comp_wind
                rospy.loginfo(f"📦 Updated cell from callback: {wind}")

                target_joints = CELL_JOINTS_ABS3.get(wind)
                self.robot.go_to_joint_abs(target_joints)
                rospy.sleep(0.5)

                cx, cy = self.latest_comp_pose
                self.robot.go_to_pose_rel([-cy, cx, 0.0],[0,0,0])
                rospy.sleep(0.5)

                self.robot.go_to_pose_rel([0.0,0.0, -0.04],[0,0,0])
                rospy.sleep(0.5)

                self.robot.grip_on()
                rospy.sleep(1)

                self.robot.go_to_joint_rel([0, radians(-8.0), 0, 0, radians(-5.0), 0])
            
                #====================================================== PLACE =====================================================================#
                self.robot.go_to_joint_abs(comp_pose_place2)
                rospy.sleep(0.5)

                self.robot.grip_off()
                rospy.sleep(1)
            
            
            if self.first == 3 :
                self.robot.go_to_joint_abs(comp_pose_place1)
                rospy.sleep(0.5)
                self.robot.go_to_pose_rel([0,0,-0.13],[0,0,0])
                rospy.sleep(0.5)
                self.robot.grip_on()
                rospy.sleep(1)
                self.robot.go_to_pose_rel([0,0,0.1],[0,0,0])
                rospy.sleep(0.5)
                self.robot.go_to_joint_abs(trash_pose)
                rospy.sleep(0.5)
                self.robot.grip_off()
                rospy.sleep(1)


            if self.second == 3 :
                self.robot.go_to_joint_abs(comp_pose_place2)
                rospy.sleep(0.5)
                self.robot.go_to_pose_rel([0,0,-0.13],[0,0,0])
                rospy.sleep(0.5)
                self.robot.grip_on()
                rospy.sleep(1)
                self.robot.go_to_pose_rel([0, 0, 0.1],[0,0,0])
                rospy.sleep(0.5)
                self.robot.go_to_joint_abs(trash_pose)
                rospy.sleep(0.5)
                self.robot.grip_off()
                rospy.sleep(1)
                




        except Exception as e:
            rospy.logerr(f"⚠️ [indy_pick_place] ERROR during iteration: {e}")
        finally:
            rospy.loginfo(f"✅ Iteration finished in {time.time() - start:.2f}s")



    def decompose_process(self):
        rospy.loginfo(f"🚀 Starting decomposition process {self.iteration_count+1}/{self.MAX_ITER})")
        start = time.time()

        try:
            #====================================================== PICK =====================================================================#
            self.robot.go_to_joint_abs(decomp_pose_place1)
            rospy.sleep(1)
            cx, cy = self.wait_until_decomp_pose_ready()

            rospy.loginfo(f"📍 Using decompose pose: cx={cx:.4f}, cy={cy:.4f}")

            self.robot.go_to_pose_rel([-cy, cx, -0.015],[0,0,0])
            rospy.sleep(0.5)
            self.robot.go_to_pose_rel([  0,  0, -0.010],[0,0,0])
            rospy.sleep(0.5)
            self.robot.grip_on()
            rospy.sleep(1)
            self.robot.go_to_pose_rel([  0,  0, 0.100],[0,0,0])
            rospy.sleep(0.5)

            #====================================================== PLACE =====================================================================#
            self.robot.go_to_joint_abs(check_pose)
            rospy.sleep(0.5)

            wind = self.latest_decomp_wind
            rospy.loginfo(f"📦 Updated wind from callback: {wind}")

            target_joints = CELL_JOINTS_ABS.get(wind)
            self.robot.go_to_joint_abs(target_joints)
            rospy.sleep(0.5)

            target_joints = CELL_JOINTS_ABS2.get(wind)
            self.robot.go_to_joint_abs(target_joints)
            rospy.sleep(0.5)

            self.robot.grip_off()
            rospy.sleep(1)

            self.robot.go_to_joint_rel([0, radians(-8.0), 0, 0, radians(-5.0), 0])
            rospy.sleep(0.5)

            #=================================================================================================================================#
            #====================================================== PICK =====================================================================#

            self.robot.go_to_joint_abs(decomp_pose_place2)
            rospy.sleep(1.0)

            cx, cy = self.latest_decomp_pose
            if not (math.isfinite(cx) and math.isfinite(cy)):
                self.open_stopper()
                return

            rospy.loginfo(f"📍 Using decompose pose: cx={cx:.4f}, cy={cy:.4f}")

            self.robot.go_to_pose_rel([-cy, cx, -0.015],[0,0,0])
            rospy.sleep(0.5)
            self.robot.go_to_pose_rel([  0,  0, -0.010],[0,0,0])
            rospy.sleep(0.5)
            self.robot.grip_on()
            rospy.sleep(1)
            self.robot.go_to_pose_rel([  0,  0, 0.100],[0,0,0])
            rospy.sleep(0.5)


            #====================================================== PLACE =====================================================================#
            self.robot.go_to_joint_abs(check_pose)
            rospy.sleep(0.5)

            wind = self.latest_decomp_wind
            rospy.loginfo(f"📦 Updated wind from callback: {wind}")

            target_joints = CELL_JOINTS_ABS.get(wind)
            self.robot.go_to_joint_abs(target_joints)
            rospy.sleep(0.5)

            target_joints = CELL_JOINTS_ABS2.get(wind)
            self.robot.go_to_joint_abs(target_joints)
            rospy.sleep(0.5)

            self.robot.grip_off()
            rospy.sleep(1)

            self.robot.go_to_joint_rel([0, radians(-8.0), 0, 0, radians(-5.0), 0])
            rospy.sleep(0.5)




        except Exception as e:
            rospy.logerr(f"⚠️ [indy_pick_place] ERROR during iteration: {e}")
        finally:
            rospy.loginfo(f"✅ Iteration finished in {time.time() - start:.2f}s")


    def run(self):
        
        self.open_stopper()
        rospy.sleep(15)
        # ====================================================================================================== #
        self.robot.go_to_joint_abs(b_arrive_check_pose)
        rospy.sleep(0.5)

        if (self.latest_bracket is None 
            or not all(math.isfinite(v) for v in self.latest_bracket)):
            self.wait_until_bracket_ready()
        
        rospy.sleep(5)

        rospy.loginfo(f"📦 Bracket is arrive")


        # ② 셀 감지 여부로 mode 판정 ============================================================================== #

        if self.process_flag not in (0, 1):
            self.wait_until_process_ready() 

        if self.process_flag == 1:
            rospy.loginfo("✅ Cell detected → compine mode selected.")
            self.compine_mode = True
        else:
            rospy.loginfo("❌ No cell detected → decompose mode selected.")
            self.compine_mode = False


        if self.compine_mode:
            self.compose_process(self.latest_comp_wind)
        else:
            self.decompose_process()


if __name__ == "__main__":
    node = IndyPickPlaceNode()
    node.run()

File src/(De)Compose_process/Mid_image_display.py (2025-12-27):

#!/usr/bin/env python3
# -*- coding:utf-8 -*-

import rospy
from sensor_msgs.msg import Image
from cv_bridge import CvBridge, CvBridgeError
import cv2
import numpy as np
from indy_driver.msg import comp_wind_info


class CellDetectorNode:
    def __init__(self):
        rospy.init_node('cell_detector', anonymous=True)
        self.bridge = CvBridge()

        # Subscriber
        self.sub_image = rospy.Subscriber("camera/image_raw", Image, self.action, queue_size=1)

        # Publisher
        self.pub_cell = rospy.Publisher("comp_wind_info", comp_wind_info, queue_size=1)

        # --- Params --- #
        self.resize_n = 600
        self.crop_x = (110, 510)
        self.crop_y = (210, 520)
        self.num_div_x = 3      # 가로 3칸
        self.num_div_y = 2      # 세로 2칸
        self.enable_viz = True

        # 🔥 주황색 범위 설정 (HSV)
        self.lower_orange = np.array([0,  80,  80])
        self.upper_orange = np.array([40, 255, 255])


        # 최소 주황색 픽셀 비율 (ROI 대비 %)
        self.orange_ratio_threshold = 0.10   # 2% 이상이면 셀 안에 물체 있다고 판단

        rospy.loginfo("✅ [cell_detector] initialized (orange-based detection)")

    def action(self, data: Image):
        try:
            cv_image = self.bridge.imgmsg_to_cv2(data, "bgr8")
        except CvBridgeError as e:
            rospy.logwarn(f"[cell_detector] CvBridgeError: {e}")
            return

        # --- Resize → HSV --- #
        n = self.resize_n
        resized = cv2.resize(cv_image, (n, n))
        hsv = cv2.cvtColor(resized, cv2.COLOR_BGR2HSV)

        # --- Crop --- #
        x_start, x_end = self.crop_x
        y_start, y_end = self.crop_y
        cropped_hsv = hsv[y_start:y_end, x_start:x_end]
        vis = resized[y_start:y_end, x_start:x_end].copy()

        # --- Grid 크기 --- #
        step_x = (x_end - x_start) // self.num_div_x
        step_y = (y_end - y_start) // self.num_div_y

        detected_cell = -1
        cell_num = 1

        # --- 셀별 주황색 픽셀 검사 --- #
        for row in range(self.num_div_y):
            for col in range(self.num_div_x):

                # ROI
                x1, y1 = col * step_x, row * step_y
                x2, y2 = x1 + step_x, y1 + step_y
                roi_hsv = cropped_hsv[y1:y2, x1:x2]

                # 주황색 마스크
                mask = cv2.inRange(roi_hsv, self.lower_orange, self.upper_orange)
                orange_pixels = np.sum(mask > 0)
                total_pixels = mask.size
                ratio = orange_pixels / total_pixels

                state = "O" if ratio > self.orange_ratio_threshold else "E"

                # 텍스트 표시
                text = f"{cell_num}:{ratio*100:.1f}%"
                color = (0, 165, 255) if state == "O" else (255, 255, 255)
                cv2.putText(vis, text, (x1 + 10, y1 + 25),
                            cv2.FONT_HERSHEY_SIMPLEX, 0.6, color, 2)

                # 가장 첫 번째로 주황색 감지된 셀 선택
                if state == "O" and detected_cell == -1:
                    detected_cell = cell_num

                cell_num += 1

        # --- 퍼블리시 --- #
        msg = comp_wind_info()
        msg.cell_num = int(detected_cell if detected_cell != -1 else 0)
        self.pub_cell.publish(msg)

        if detected_cell == -1:
            rospy.loginfo("[cell_detector] publish: cell=0 (no orange detected)")
        else:
            rospy.loginfo(f"[cell_detector] publish: cell={msg.cell_num} (orange detected)")

        # --- 시각화 --- #
        if self.enable_viz:
            # Grid 라인
            for i in range(1, self.num_div_x):
                cv2.line(vis, (i * step_x, 0), (i * step_x, vis.shape[0]), (0, 255, 0), 2)
            for j in range(1, self.num_div_y):
                cv2.line(vis, (0, j * step_y), (vis.shape[1], j * step_y), (0, 255, 0), 2)

            cv2.imshow("Image Display1: Orange Cell Detection", vis)
            cv2.waitKey(1)

    def run(self):
        rospy.spin()


if __name__ == '__main__':
    try:
        node = CellDetectorNode()
        node.run()
    except rospy.ROSInterruptException:
        pass

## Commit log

2025-12-27 Update README with Arduino and camera connection steps
    Add instructions for connecting Arduino and camera.
2025-12-28 README.md 업데이트
